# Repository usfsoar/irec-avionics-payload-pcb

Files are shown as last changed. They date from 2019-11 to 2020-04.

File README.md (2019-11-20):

# IREC Avionics Payload PCB

This is the PCB for the payload of USF Society of Aeronautics and Rocketry's 2019 IREC rocket. The PCB is made in KiCad (pronounced key-cad). The different two parts of the payload are split into the folders ***payload_ground_pcb***, the ground station, and ***payload_main_pcb***, the cubesat payload, under those there are the files are:

* ***avionics-\*.pro*** - This is the base project which you should open in KiCad.
* ***avionics-\*.sch*** - This is the sketch of the PCB and shows which components should be connected where.
* ***avionics-\*.kicad_pcb*** - This is the actual PCB that has the components laid out and connected with physical dimensions.
* ***components*** - This folder contains components that are not by default included with KiCad

## About the board

The main components of the Cubesat Payload are:

* [Teensy 4.0](https://www.pjrc.com/store/teensy40.html) - This small Arduino compatible board is very powerful for its size with 600 MHz, 1M RAM, and 2M Flash as well as lots of connectivity options.
* [MS5607](https://www.te.com/commerce/DocumentDelivery/DDEController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) - This is the barometric sensor for the board, it provides high resolution and low pressure while being inexpensive and having a digital interface.
* [ADIS16470](https://www.analog.com/media/en/technical-documentation/data-sheets/ADIS16470.pdf) - This is the inertial measurement unit  which measures acceleration and direction. This highend component will provide an accurate and precice measurments and is the core of the payloads ability to be tracked in realtime by the ground station.
* [SAM M8Q](https://www.u-blox.com/sites/default/files/SAM-M8Q_DataSheet_%28UBX-16012619%29.pdf) - This is the GPS module and it provides a built in antenna and a digital interface.
* [RFM95W](https://cdn.sparkfun.com/assets/learn_tutorials/8/0/4/RFM95_96_97_98W.pdf) - For now this is a temporary RF module that will stand in for what ever RF solution is decided while testing. It provides many benefits for this purpose such as being in the 915MHz range and having long enough range that if necessary it could be used for launch.

The main components of the Ground Station are:

* Teensy 4.0
* SAM M8Q
* RFM95W

## How to contribute

KiCad is a free and open source software that is available on most desktop OSs. To learn how to use KiCad [here](https://github.com/MalphasWats/hawk) is a pretty great tutorial that goes through making a simple PCB. You can go at your own pace but it should take about an hour but after that you should have a pretty good understanding of KiCad.

If you want to add-on to the board the best way would be to create a hierarchical sheet if you are adding on a new subsystem or if you are adjusting the main board try not to adjust (move, rename, etc) items that you do not plan to change.

If you haven't used Git or GitHub before (or you have and just want the commands to make a pull request for this repository) go [here](https://github.com/usfsoar/irec-avionics-payload-pcb/blob/master/git_instructions.md).

## Pictures

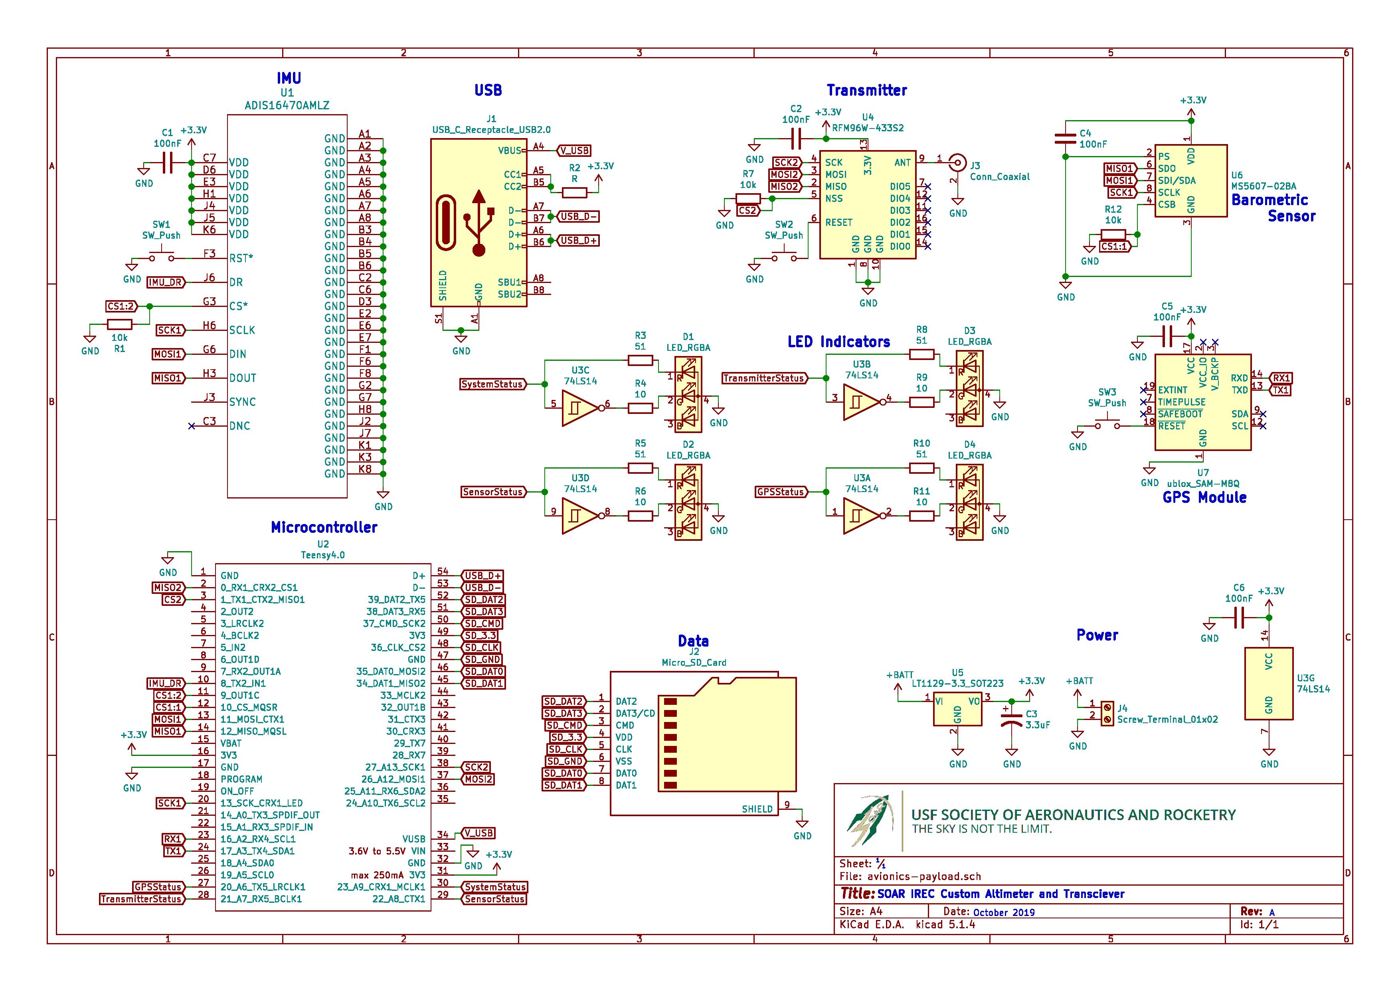
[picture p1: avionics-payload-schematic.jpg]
Schematic


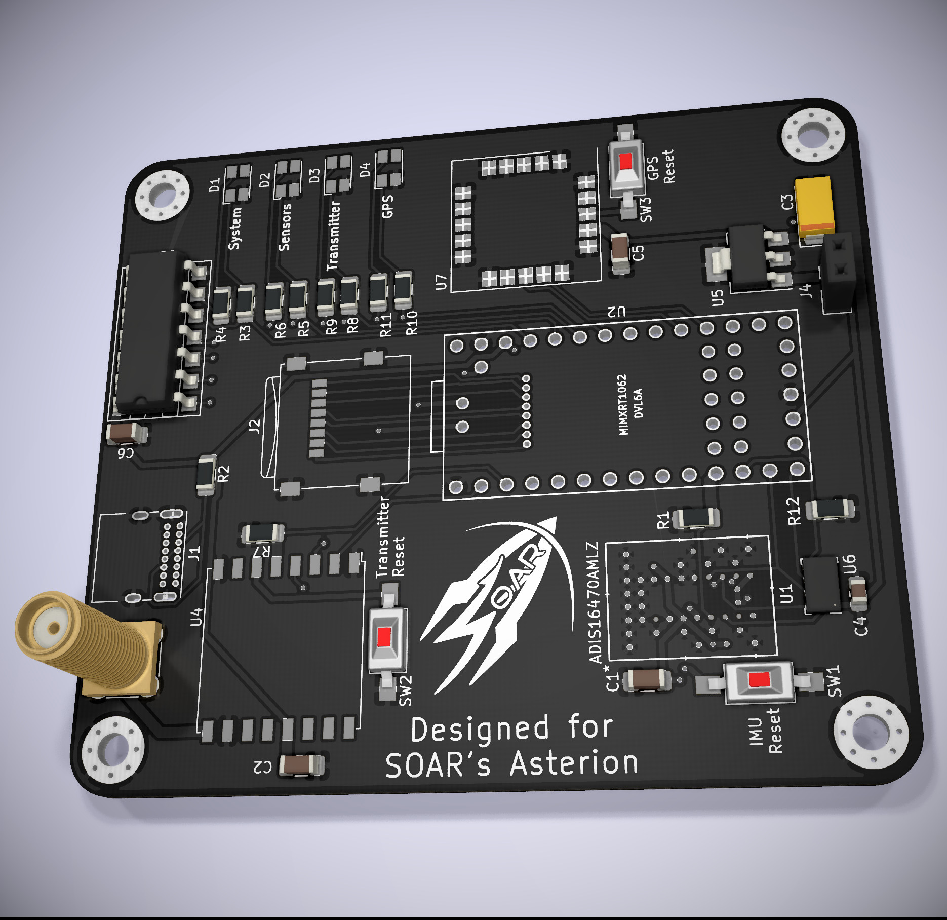
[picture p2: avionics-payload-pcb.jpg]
PCB


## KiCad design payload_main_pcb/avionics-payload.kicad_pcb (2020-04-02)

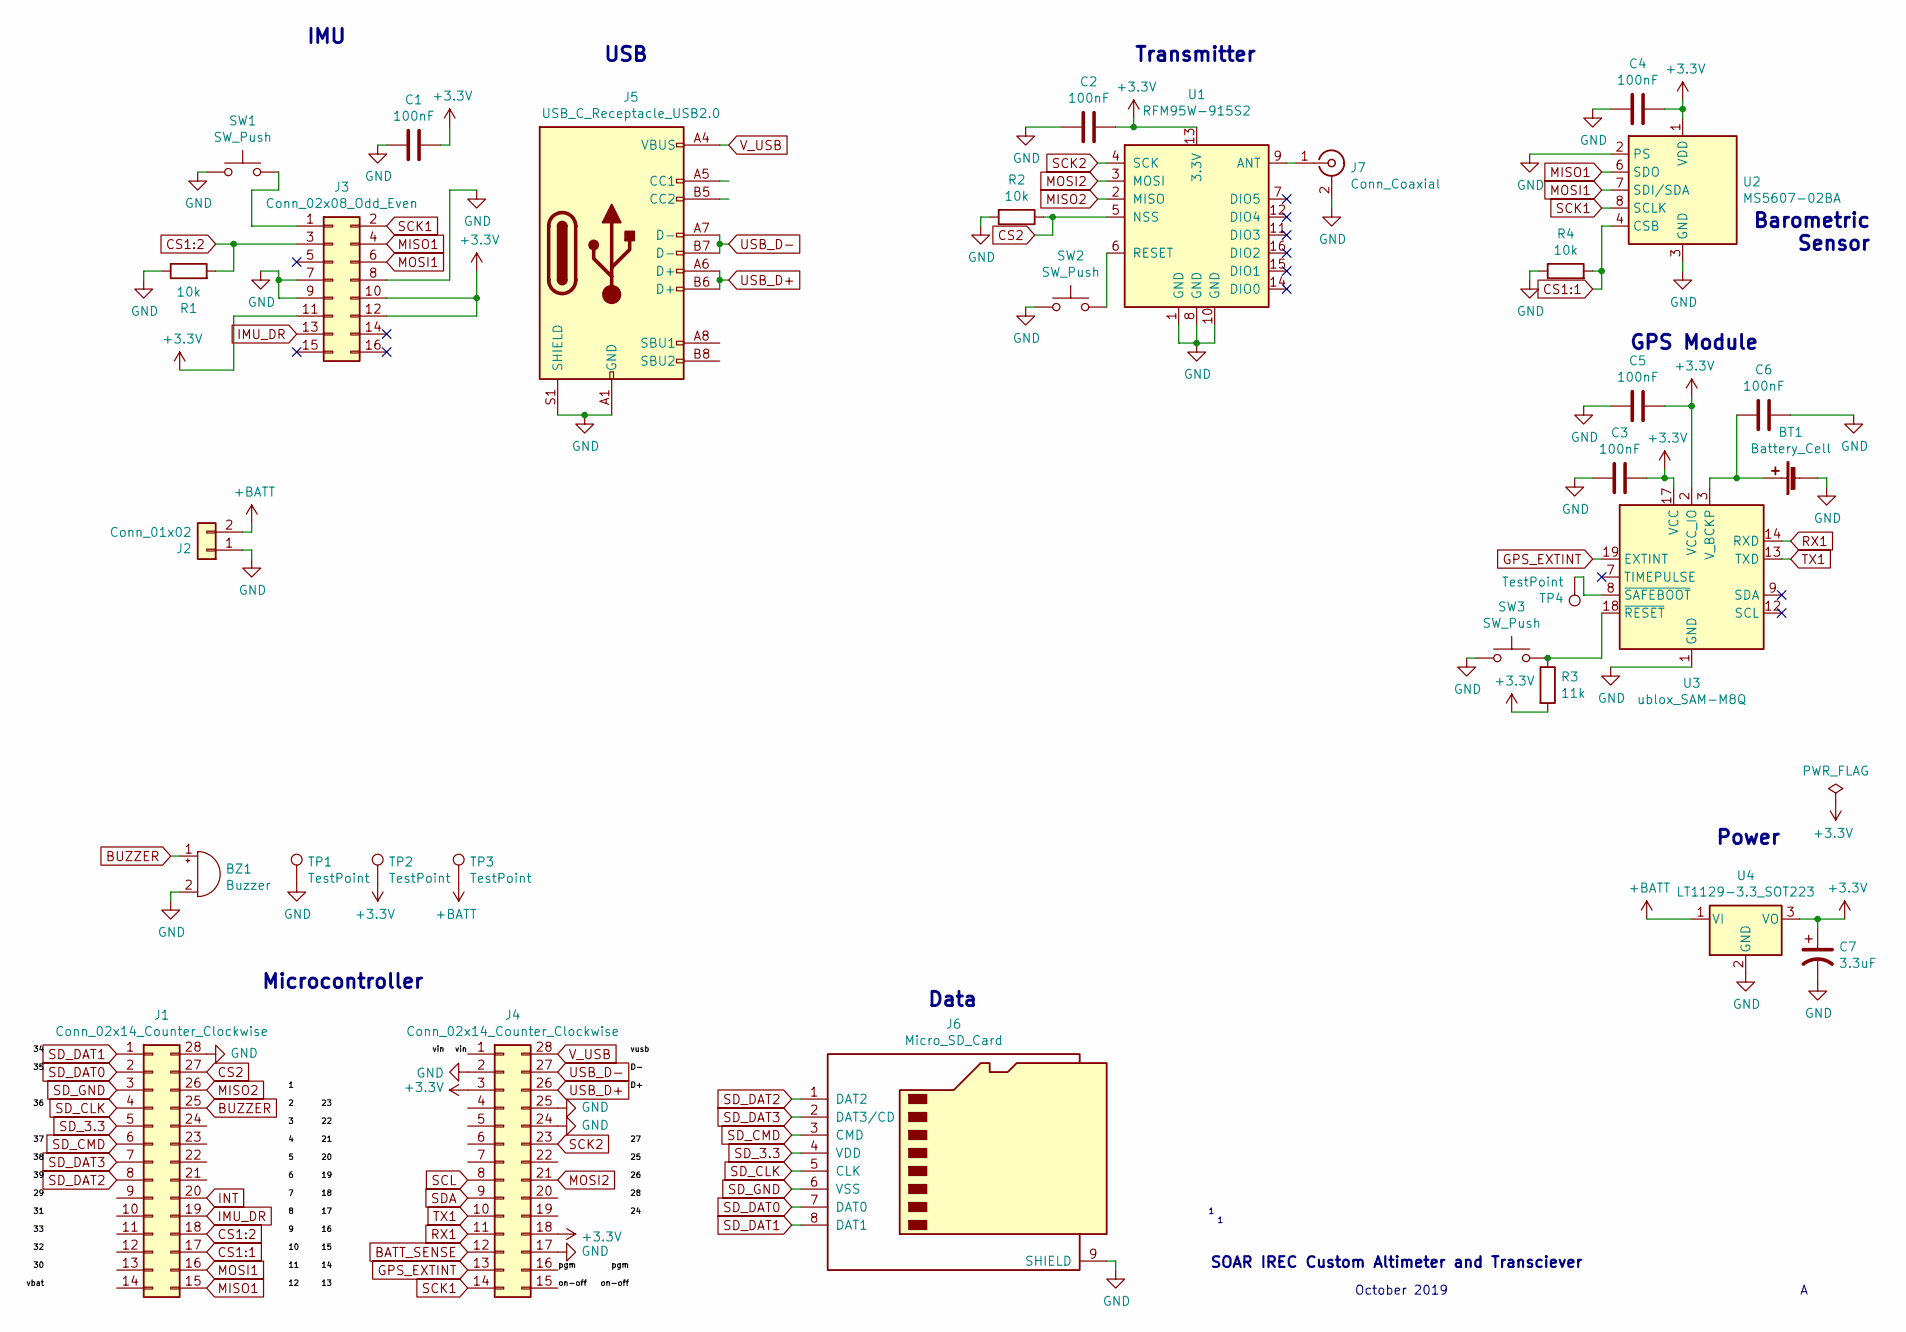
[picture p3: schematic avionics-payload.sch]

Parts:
BT1: Battery_Cell; BatteryHolder_Keystone_1060_1x2032
BZ1: Buzzer; Buzzer_CUI_CPT-9019S-SMT
C1, C2, C3, C4, C5, C6: 100nF; C_1206_3216Metric_Pad1.42x1.75mm_HandSolder
C7: 3.3uF; CP_Elec_4x3.9
J1, J4: Conn_02x14_Counter_Clockwise; PinSocket_2x14_P2.54mm_Vertical
J2: Conn_01x02; TerminalBlock_bornier-2_P5.08mm
J3: Conn_02x08_Odd_Even; PinHeader_2x08_P2.00mm_Vertical_SMD
J5: USB_C_Receptacle_USB2.0; USB_C_Receptacle_GCT_USB4085
J6: Micro_SD_Card; microSD_HC_Wuerth_693072010801
J7: Conn_Coaxial; SMA_Amphenol_132291_Vertical
R1, R2, R4: 10k; R_1206_3216Metric_Pad1.42x1.75mm_HandSolder
R3: 11k; R_1206_3216Metric_Pad1.42x1.75mm_HandSolder
SW1, SW2, SW3: SW_Push; SW_SPST_FSMSM
TP1, TP2, TP3: TestPoint; TestPoint_Loop_D2.50mm_Drill1.0mm
TP4: TestPoint; Pin_D1.0mm_L10.0mm
U1: RFM95W-915S2; HOPERF_RFM9XW_SMD
U2: MS5607-02BA; LGA-8_3x5mm_P1.25mm
U3: ublox_SAM-M8Q
U4: LT1129-3.3_SOT223; SOT-223-3_TabPin2

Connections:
+3V3: C1.1, C2.1, C3.1, C4.1, C5.1, C7.1, J3.10, J3.11, J3.12, J4.3, J4.18, R3.2, TP2.1, U1.13 (3.3V), U2.1 (VDD), U3.2 (VCC_IO), U3.17 (VCC), U4.3 (VO)
+BATT: J2.2, TP3.1, U4.1 (VI)
/on-off: J4.15
/pgm: J4.16
/vin: J4.1
BATT_SENSE: J4.12
BUZZER: BZ1.1 (-), J1.25
CS1:1: J1.17, R4.2, U2.4 (CSB), U2.5 (CSB)
CS1:2: J1.18, J3.3, R1.2
CS2: J1.27, R2.1, U1.5 (NSS)
GND: BT1.2 (-), BZ1.2 (+), C1.2, C2.2, C3.2, C4.2, C5.2, C6.1, C7.2, J1.28, J2.1, J3.7, J3.8, J3.9, J4.2, J4.17, J4.24, J4.25, J5.A1 (GND), J5.A12 (GND), J5.B1 (GND), J5.B12 (GND), J5.S1 (SHIELD), J6.9 (SHIELD), J7.2 (Ext), R1.1, R2.2, R4.1, SW1.1, SW2.1, SW3.1, TP1.1, U1.1 (GND), U1.8 (GND), U1.10 (GND), U2.2 (PS), U2.3 (GND), U3.1 (GND), U3.4 (GND), U3.5 (GND), U3.6 (GND), U3.10 (GND), U3.11 (GND), U3.15 (GND), U3.16 (GND), U3.20 (GND), U4.2 (GND)
GPS_EXTINT: J4.13, U3.19 (EXTINT)
IMU_DR: J1.19, J3.13
INT: J1.20
MISO1: J1.15, J3.4, U2.6 (SDO)
MISO2: J1.26, U1.2 (MISO)
MOSI1: J1.16, J3.6, U2.7 (SDI/SDA)
MOSI2: J4.21, U1.3 (MOSI)
unnamed: BT1.1 (+), C6.2, U3.3 (V_BCKP)
unnamed: J3.1, SW1.2
unnamed: J7.1 (In), U1.9 (ANT)
unnamed: R3.1, SW3.2, U3.18 (~RESET)
unnamed: SW2.2, U1.6 (RESET)
unnamed: TP4.1, U3.8 (~SAFEBOOT)
RX1: J4.11, U3.14 (RXD)
SCK1: J3.2, J4.14, U2.8 (SCLK)
SCK2: J4.23, U1.4 (SCK)
SCL: J4.8
SDA: J4.9
SD_3.3: J1.5, J6.4 (VDD)
SD_CLK: J1.4, J6.5 (CLK)
SD_CMD: J1.6, J6.3 (CMD)
SD_DAT0: J1.2, J6.7 (DAT0)
SD_DAT1: J1.1, J6.8 (DAT1)
SD_DAT2: J1.8, J6.1 (DAT2)
SD_DAT3: J1.7, J6.2 (DAT3/CD)
SD_GND: J1.3, J6.6 (VSS)
TX1: J4.10, U3.13 (TXD)
USB_D+: J4.26, J5.A6 (D+), J5.B6 (D+)
USB_D-: J4.27, J5.A7 (D-), J5.B7 (D-)
V_USB: J4.28, J5.A4 (VBUS), J5.A9 (VBUS), J5.B4 (VBUS), J5.B9 (VBUS)

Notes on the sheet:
SOAR IREC Custom Altimeter and Transciever
October 2019
Transmitter
GPS Module
Power
Barometric Sensor
Data
IMU
USB
Microcontroller

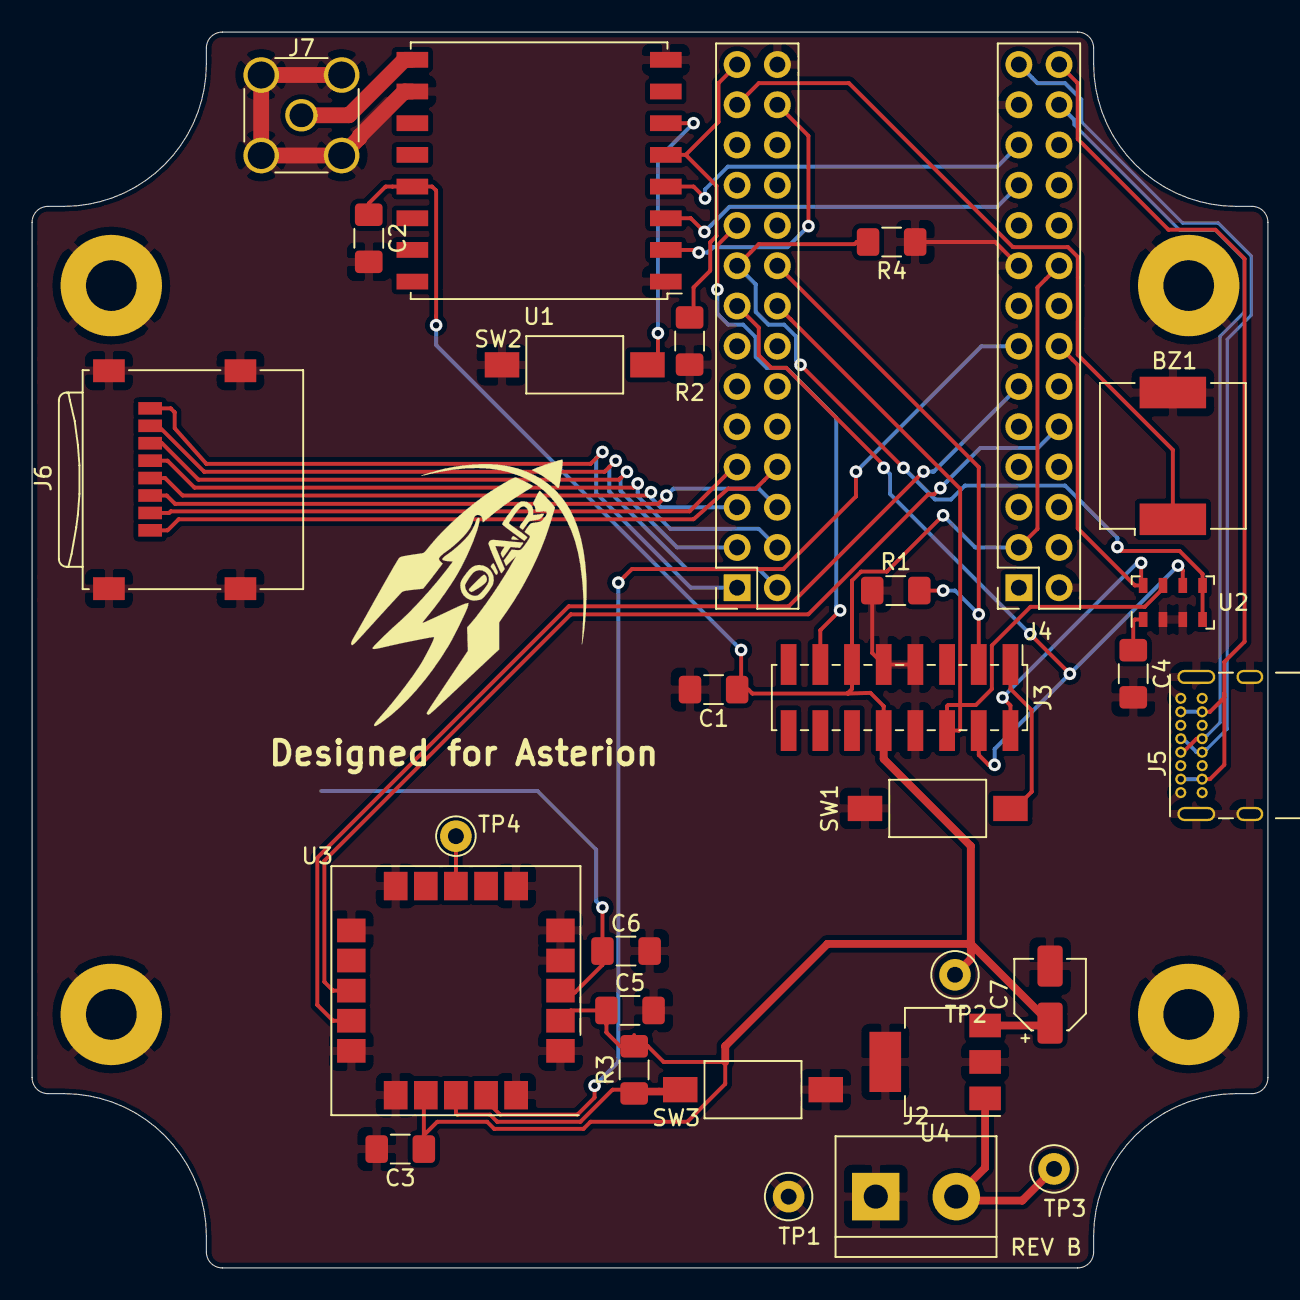
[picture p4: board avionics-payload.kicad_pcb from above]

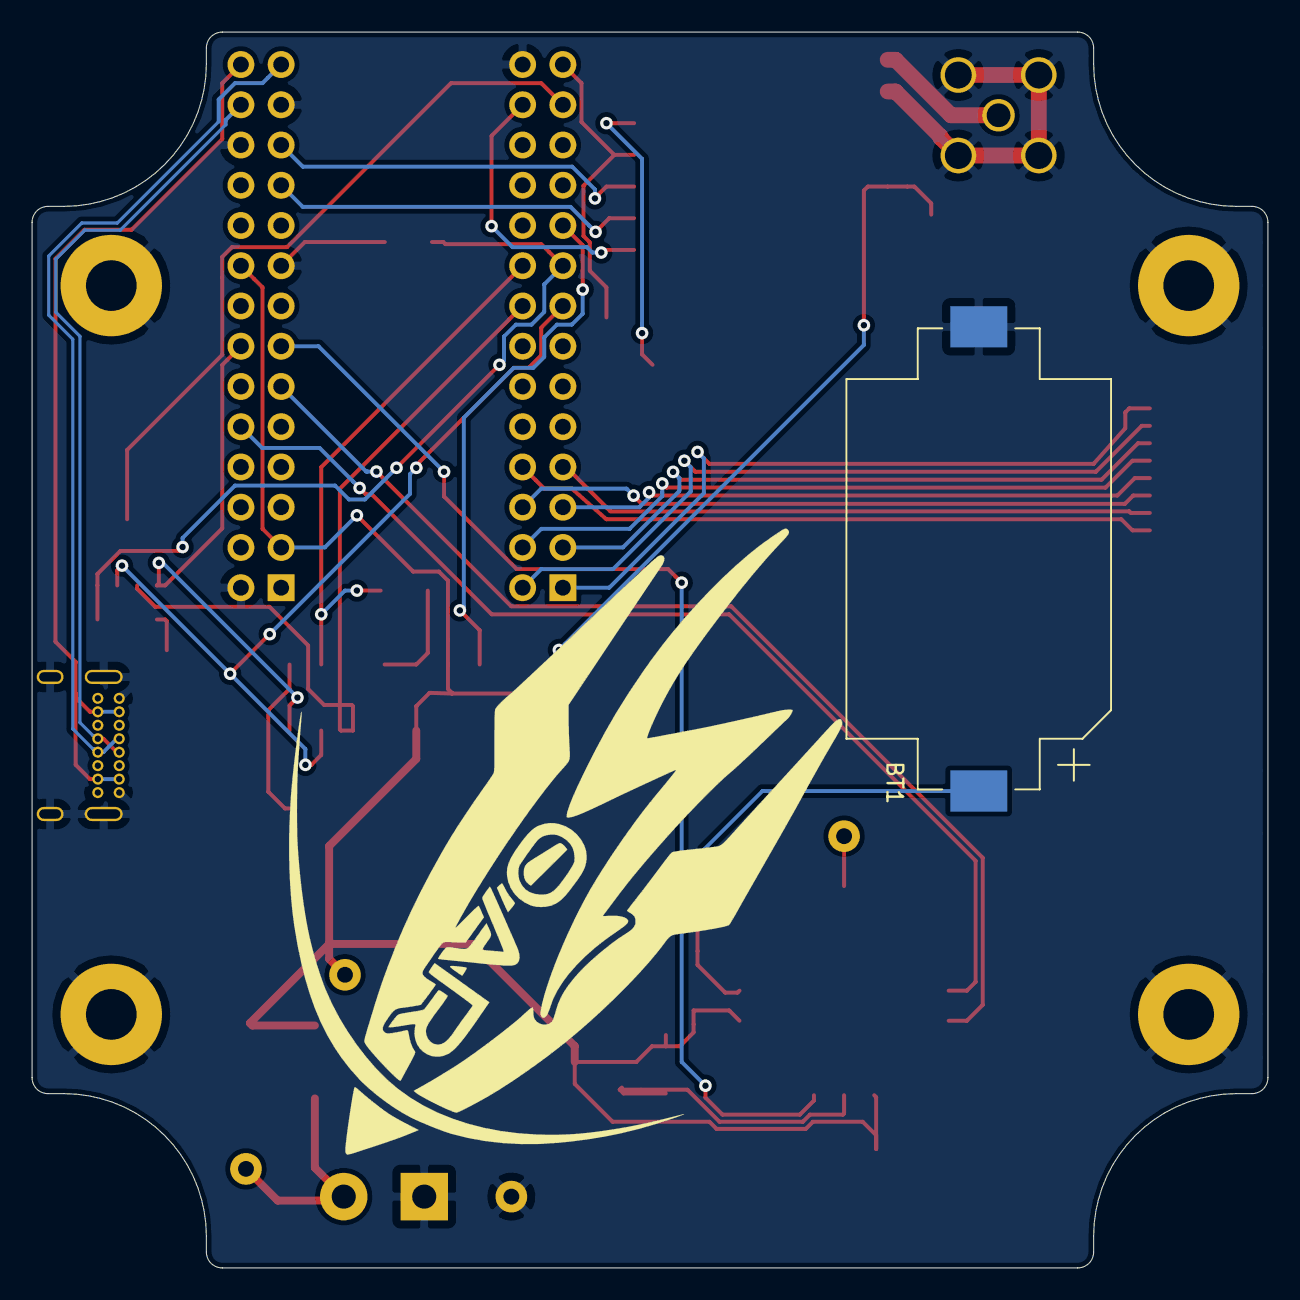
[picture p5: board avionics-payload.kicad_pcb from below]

Board: 2 copper layers, 78.0 x 78.0 mm, 33 parts (2 on the bottom side), 34 nets.

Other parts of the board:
Ref**: Val**; drawing
Ref**#2: Val**; logo

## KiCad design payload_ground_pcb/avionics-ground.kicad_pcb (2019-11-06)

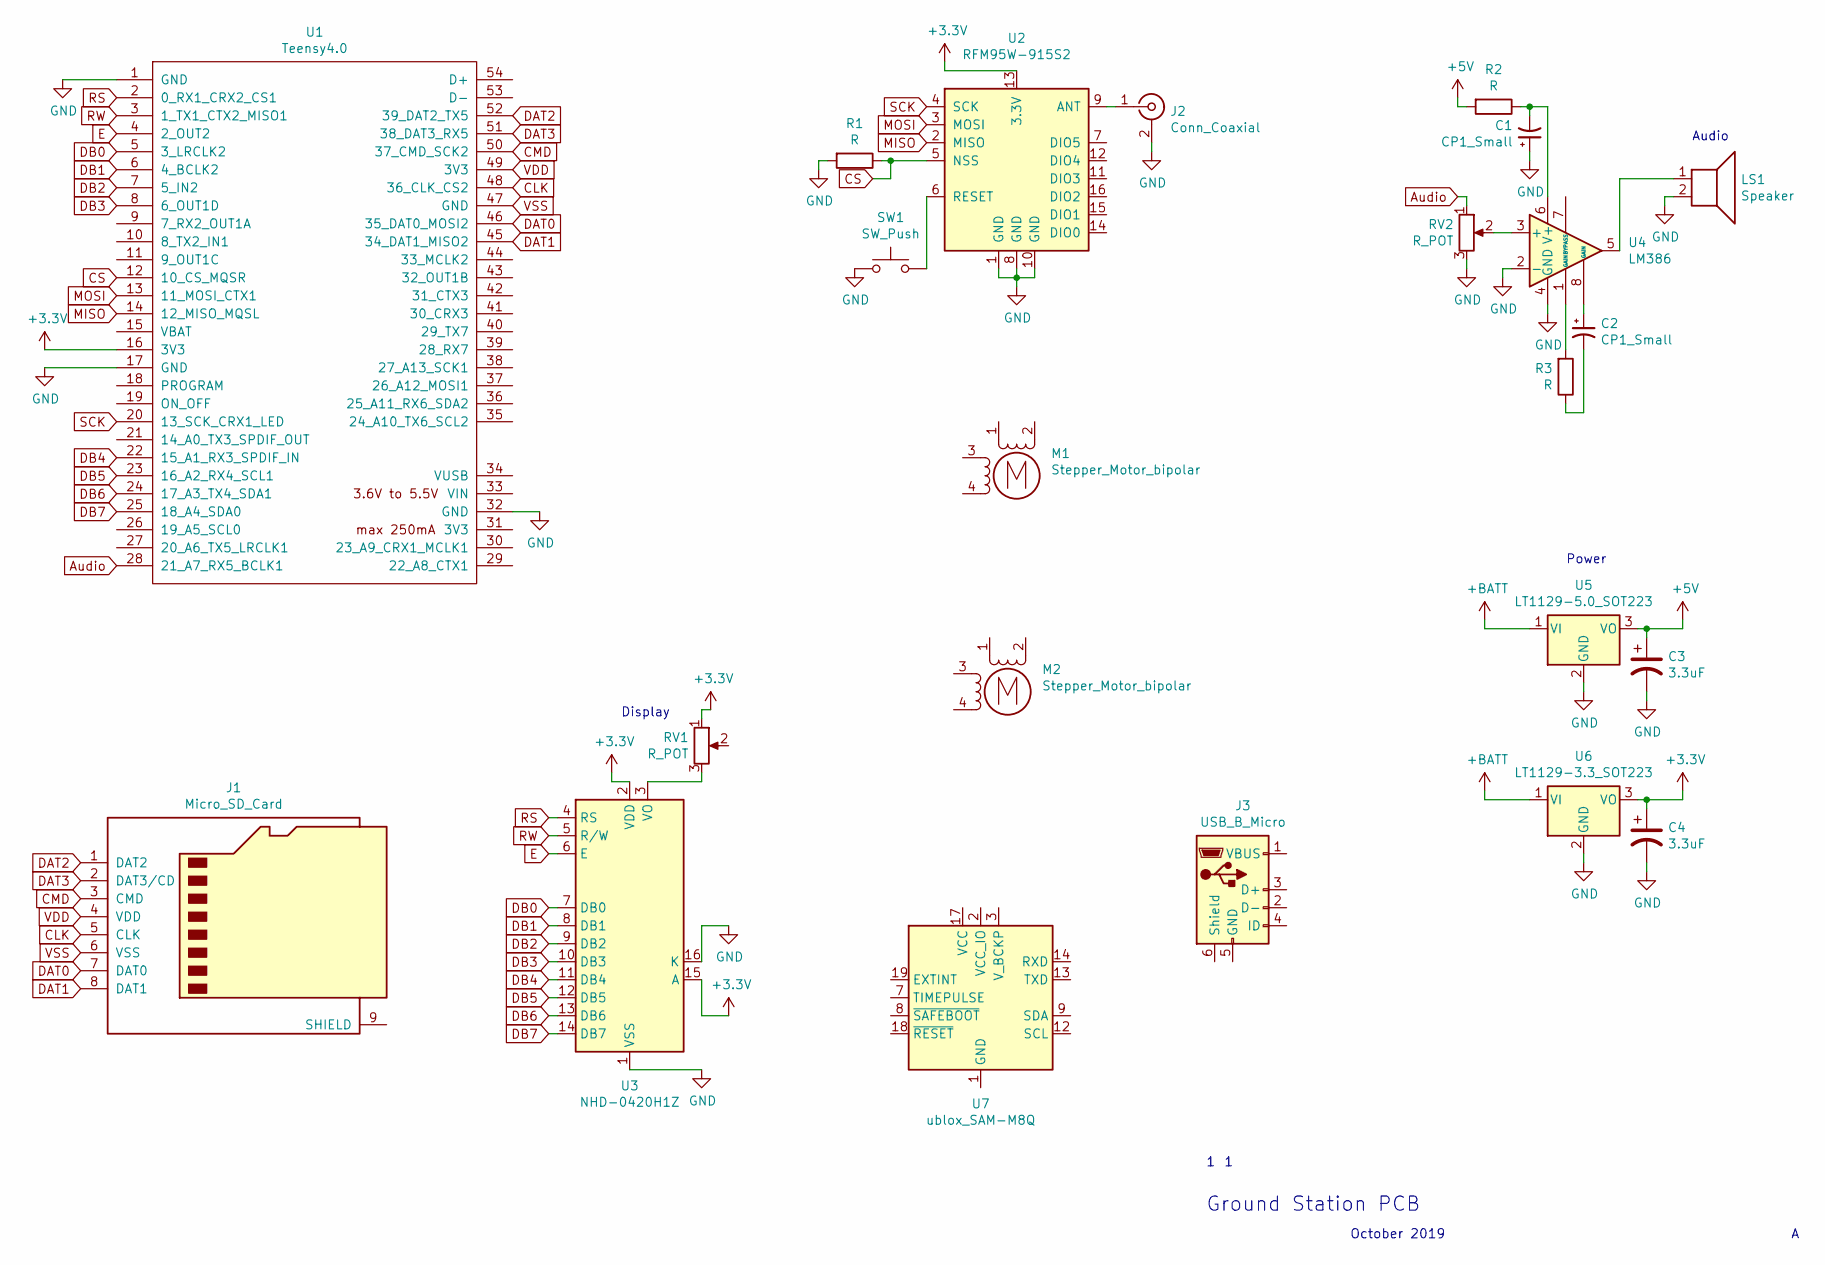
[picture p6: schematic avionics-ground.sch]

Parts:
C1, C2: CP1_Small; CP_EIA-1608-08_AVX-J_Pad1.25x1.05mm_HandSolder
C3, C4: 3.3uF; CP_EIA-1608-08_AVX-J_Pad1.25x1.05mm_HandSolder
J1: Micro_SD_Card; microSD_HC_Wuerth_693072010801
J2: Conn_Coaxial; SMA_Amphenol_132134-14_Vertical
J3: USB_B_Micro; USB_Mini-B_Lumberg_2486_01_Horizontal
LS1: Speaker; Buzzer_Murata_PKMCS0909E4000-R1
M1, M2: Stepper_Motor_bipolar
R1, R2, R3: R; R_0805_2012Metric_Pad1.15x1.40mm_HandSolder
RV1, RV2: R_POT; Potentiometer_ACP_CA6-VSMD_Vertical_Hole
SW1: SW_Push; SW_PUSH_6mm
U1: Teensy4.0; Teensy40
U2: RFM95W-915S2; HOPERF_RFM9XW_SMD
U3: NHD-0420H1Z
U4: LM386; DIP-8_W7.62mm_SMDSocket_SmallPads
U5: LT1129-5.0_SOT223; SOT-223-3_TabPin2
U6: LT1129-3.3_SOT223; SOT-223-3_TabPin2
U7: ublox_SAM-M8Q

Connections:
+3V3: C4.1, RV1.1, U1.16 (3V3), U2.13 (3.3V), U3.2 (VDD), U3.15 (A), U6.3 (VO)
+5V: C3.1, R2.2, U5.3 (VO)
+BATT: U5.1 (VI), U6.1 (VI)
Audio: RV2.1, U1.28 (21_A7_RX5_BCLK1)
CLK: J1.5 (CLK), U1.48 (36_CLK_CS2)
CMD: J1.3 (CMD), U1.50 (37_CMD_SCK2)
CS: R1.1, U1.12 (10_CS_MQSR), U2.5 (NSS)
DAT0: J1.7 (DAT0), U1.46 (35_DAT0_MOSI2)
DAT1: J1.8 (DAT1), U1.45 (34_DAT1_MISO2)
DAT2: J1.1 (DAT2), U1.52 (39_DAT2_TX5)
DAT3: J1.2 (DAT3/CD), U1.51 (38_DAT3_RX5)
DB0: U1.5 (3_LRCLK2), U3.7 (DB0)
DB1: U1.6 (4_BCLK2), U3.8 (DB1)
DB2: U1.7 (5_IN2), U3.9 (DB2)
DB3: U1.8 (6_OUT1D), U3.10 (DB3)
DB4: U1.22 (15_A1_RX3_SPDIF_IN), U3.11 (DB4)
DB5: U1.23 (16_A2_RX4_SCL1), U3.12 (DB5)
DB6: U1.24 (17_A3_TX4_SDA1), U3.13 (DB6)
DB7: U1.25 (18_A4_SDA0), U3.14 (DB7)
E: U1.4 (2_OUT2), U3.6 (E)
GND: C1.1, C3.2, C4.2, J2.2 (Ext), LS1.2, R1.2, RV2.3, SW1.1, U1.1 (GND), U1.17 (GND), U1.32 (GND), U2.1 (GND), U2.8 (GND), U2.10 (GND), U3.1 (VSS), U3.16 (K), U4.2 (-), U4.4 (GND), U5.2 (GND), U6.2 (GND)
MISO: U1.14 (12_MISO_MQSL), U2.2 (MISO)
MOSI: U1.13 (11_MOSI_CTX1), U2.3 (MOSI)
unnamed: C1.2, R2.1, U4.6 (V+)
unnamed: C2.1, U4.8 (GAIN)
unnamed: C2.2, R3.1
unnamed: J2.1 (In), U2.9 (ANT)
unnamed: LS1.1, U4.5
unnamed: R3.2, U4.1 (GAIN)
unnamed: RV1.3, U3.3 (VO)
unnamed: RV2.2, U4.3 (+)
unnamed: SW1.2, U2.6 (RESET)
unnamed: U7.1 (GND), U7.4 (GND), U7.5 (GND), U7.6 (GND), U7.10 (GND), U7.11 (GND), U7.15 (GND), U7.16 (GND), U7.20 (GND)
RS: U1.2 (0_RX1_CRX2_CS1), U3.4 (RS)
RW: U1.3 (1_TX1_CTX2_MISO1), U3.5 (R/W)
SCK: U1.20 (13_SCK_CRX1_LED), U2.4 (SCK)
VDD: J1.4 (VDD), U1.49 (3V3)
VSS: J1.6 (VSS), U1.47 (GND)

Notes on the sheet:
Power
Audio
Ground Station PCB
October 2019
Display

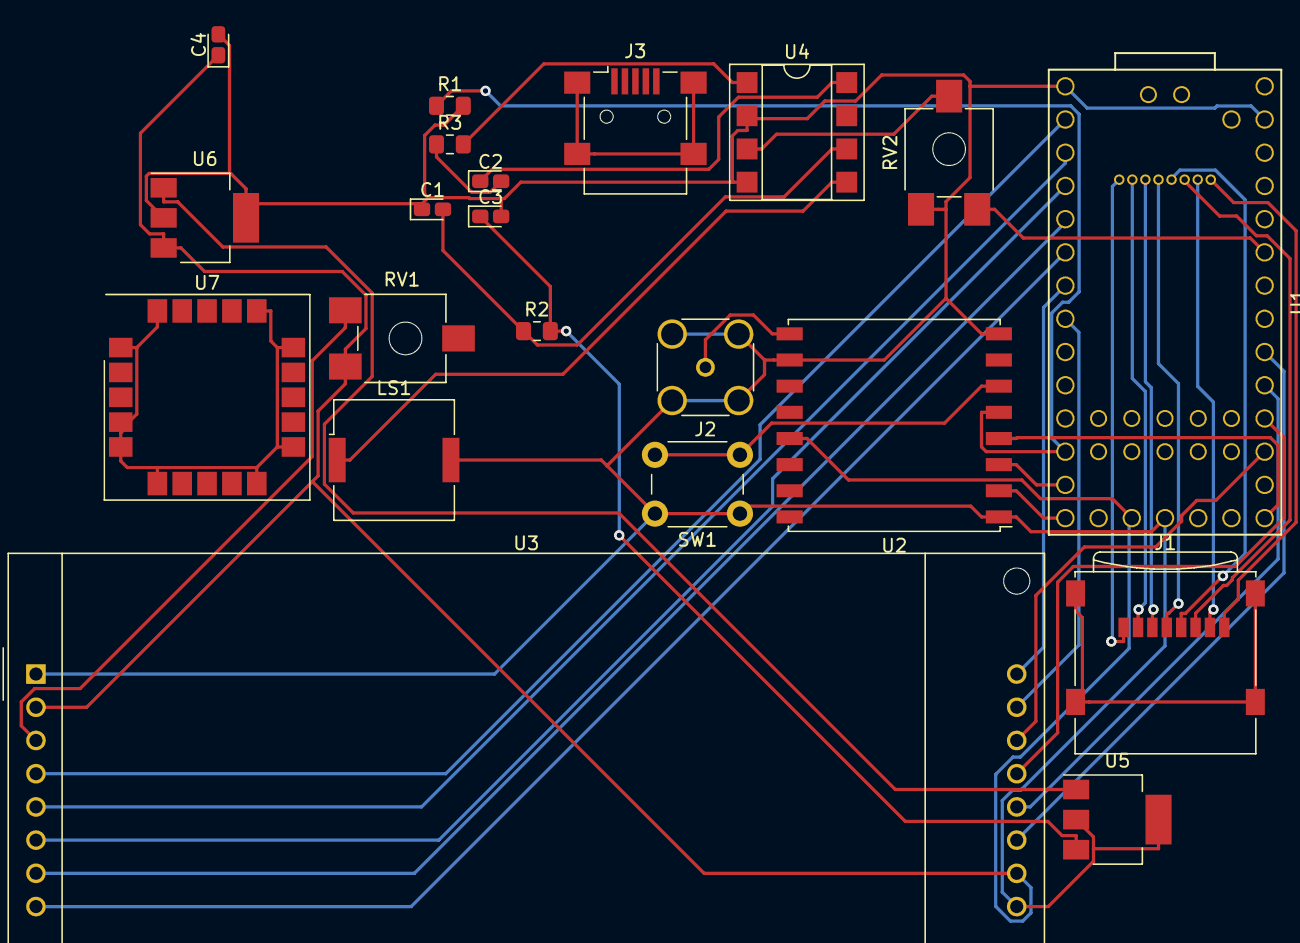
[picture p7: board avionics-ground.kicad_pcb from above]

Board: 2 copper layers, 21 parts (0 on the bottom side), 38 nets.

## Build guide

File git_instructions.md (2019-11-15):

# How to contribute using Git and GitHub

## Step 0: Be a member of the SOAR GitHub Team

If you are not a member already message Ian Sanders or Madison Kozee on Slack
with your GitHub username and say you want to be on the IREC team.

## Step 1: Download Git

Go [here](https://www.git-scm.com/downloads) and download the version for your
OS. If on Linux use your distros package manager.

## Step 2: Open your terminal

* **Windows** - Open *Git Bash*
* **MacOS/Linux** - Open *Terminal*

## Step 3: Configure Git

Run both of these commands and substitute `<username>` and `<email>` with your
GitHub username and email. The brackets are replaced as well so it will just be
your username in parentheses.

```
git config --global user.name "<username>"
git config --global user.email "<email>"
```

## Step 4: Navigate to where files will be stored

If you want the main directory **irec-avionics-payload-pcb** to be in **Documents**
then run `cd Documents`

## Step 5: Clone the project

```
git clone https://github.com/usfsoar/irec-avionics-payload-pcb.git
```

## Step 6: Navigate into the cloned directory and make sure you have no uncommited changes

```
cd irec-avionics-payload-pcb
```

Then run `git status`, if there are any changes untracked files, changes not
staged for commit, or stanged items run `git stash`.

## Step 7: Create a new branch for your feature

Replace `<name_of_branch>` with a short but discriptive name of the feature you
are working on. Note, you will be prompted for your GitHub password and username
at this step.

```
git pull
git checkout -b <name_of_branch>
git push origin <name_of_branch>
```

## Step 8: Edit the files for your feature/change

Make all of the edits to the project here before you go to the next step

## Step 9: Commiting changes

Replace `<git_commit_message>` with a discription of what changes you made so
it is clear what the changes to the project are

```
git add .
git commit -m "<git_commit_message>"
```

## Step 10: Push branch to GitHub

Push your branch to GitHub, make sure to keep the branch name consistant by
replcing the `<name_of_branch>` with the same name of the branch from earlier

```
git push -u origin <name_of_branch>
```

## Step 11: Pull Request

Now go to the GitHub project pull request page
[here](https://github.com/usfsoar/irec-avionics-payload-pcb/pulls) and make a
pull request saying what you changed and why it should be part of the project.

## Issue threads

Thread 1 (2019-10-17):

Check payload PCB for correctness

grant0417, 2019-10-17:
Look at the payload PCB and cross check with datasheets as well as other resources to make sure design is reasonable and correct. Report back to this issue with findings.

Closed 2021-10-16.

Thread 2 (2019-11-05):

Replace ADXL357 with ADIS16470

grant0417, 2019-11-05:
Hookup the ADIS using the same SPI ports as the ADXL

https://www.analog.com/media/en/technical-documentation/data-sheets/ADIS16470.pdf

Closed 2019-11-19.

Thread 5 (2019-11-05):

Research stepper and stepper drivers for Ground Station Yagi

grant0417, 2019-11-05:
Research what type of stepper and stepper driver will be needed to move the Yagi on the ground to point at the antenna. Doing calculations of how fast the steppers need to move also.

Closed 2021-10-16.

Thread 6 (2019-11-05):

USB and UART-to-USB

grant0417, 2019-11-05:
Switch USB Micro to be USB C and connect to FT232RL so the Teensy can be connected to a computer.

Closed 2021-10-16.

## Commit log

2019-10-11 Added links to KiCad site
2019-10-11 Added more on how to get using KiCad
2019-10-12 Added power module and made schematic more modular.
    [avionics-payload.kicad_pcb, avionics-payload.sch]
2019-10-13 Moved files to folders and started ground station
    [avionics-ground.kicad_pcb, avionics-ground.sch, avionics-payload.kicad_pcb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]
2019-10-13 Added SD card
    [avionics-payload.sch]
2019-10-15 Work on ground station and new IMU added to payload
    [avionics-ground.kicad_pcb, avionics-ground.sch, avionics-payload.kicad_pcb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]
2019-10-16 Added data module
    [avionics-payload.sch]
2019-10-17 Added logo to board
    [avionics-payload.kicad_pcb]
2019-11-06 Wired boards using autorouter
    [avionics-ground.kicad_pcb, avionics-ground.sch, avionics-payload.kicad_pcb]
2019-11-15 Integrated ADIS16470 in schematic and removed ADXL357
    [avionics-payload.kicad_pcb, avionics-payload.sch]
2019-11-19 Lots of stuff
    [avionics-payload.kicad_pcb, avionics-payload.sch]
2019-11-20 Changed buttons and added bottom plane
    [avionics-payload.kicad_pcb]
2019-11-27 PCB REV A
    [avionics-payload.kicad_pcb, avionics-payload.sch]
2020-04-02 REV B
    [avionics-ground.sch, avionics-payload.kicad_pcb, avionics-payload.sch]
